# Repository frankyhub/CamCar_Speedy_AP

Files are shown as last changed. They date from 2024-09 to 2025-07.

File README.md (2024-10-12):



<div align="center">

|[:skull:ISSUE](https://github.com/frankyhub/CamCar_Speedy_AP/issues?q=is%3Aissue)|[:speech_balloon: Forum /Discussion](https://github.com/frankyhub/CamCar_Speedy_AP/discussions)|[:grey_question:WiKi](https://github.com/frankyhub/CamCar_Speedy_AP/wiki)||
|--|--|--|--|
| | | | |
||<a href="https://github.com/frankyhub/CamCar_Speedy_AP/issues">|<a href="https://github.com/frankyhub/CamCar_Speedy_AP/discussions">|<a href="https://github.com/frankyhub/CamCar_Speedy_AP/releases">|
|| <a href="https://github.com/frankyhub/CamCar_Speedy_AP/pulse" alt="Activity">| <a href="https://github.com/frankyhub/CamCar_Speedy_AP/graphs/traffic">  |<a href="https://github.com/frankyhub?tab=stars"> |
</div>

## Story

Diese Anleitung beschreibt ein Remote Controlled Car Robot mit Handy-Steuerung und Web-Cam. Der Antrieb erfolgt über zwei Getriebe-Motore, als Spannungversorgung dienen zwei Akkus oder optional eine Powerbank bzw. eine 9V-Batterie. Das Herzstrück ist ein ESP32-CAM, die Bodenplatte wird aus einer 4mm Sperrholzplatte gelasert. Nach anlegen der Versorgungsspannung startet das Programm mit einem Access Point (AP). Der AP wird in den WLAN-Einstellungen des Handy/Tablet aufgerufen und danach mit der IP-Adresse 192.168.4.1 der WEB-Server im Browser gestartet. Mit dem WEB-Server steht das Kammerabild und die Motor-Steuer-Buttons zur Verfügung.

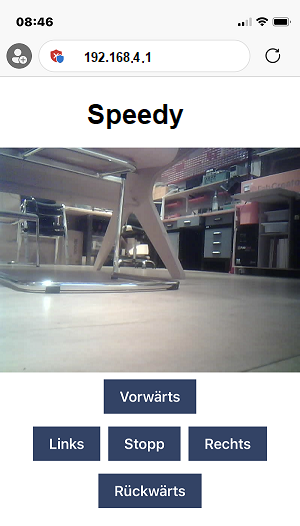
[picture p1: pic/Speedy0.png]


## Hardware

Die Stückliste für das CamCar:

| Anzahl | Bezeichnung | 
| --- | --- |
|  1 |  ESP32-CAM  |
|  1 |  ESP32-CAM Shield  |
| 1  |  Sperrholzplatte DINA4 4mm |
|  8 |  Platinenhalter (3D-Druck)  |
| 2  |  Getriebemotore mit Räder  |
| 1  |  Lenkrolle mit Abstandsplatte  |
| 1  | Schalter |
| 1  |  Dual-H-Brücke-DC-Motorantrieb L298N  |
| 2  |  18650 Akkus mit Akkucase (optional eine Powerbank oder 9V Batterie)  |
| |  Kleinmaterial, Schrauben, Muttern, Klemmen, Platinenstecker, Schaltdraht  |
| ---  | --- |

## Aufbau und Montage

Der Aufbau und die Montage des CamCars ist in mehrere Schritte unterteilt.

Schritt 1: Die Sperrholzplatte lasern

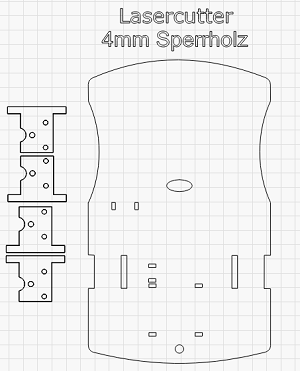
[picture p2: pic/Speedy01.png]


Schritt 2: Acht Platinenhalter drucken.

Die Platinenhalter tragen den ESP32 und die H-Brücke. Sie werden auf die Bodenplatte geklebt.

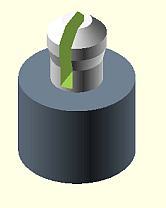
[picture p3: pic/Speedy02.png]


Schritt 3: Die vier Getriebemotore auf die Bodenplatte montieren (Senkkopfschrauben M3x30).

Die Lötfahnen zeigen jeweils nach innen.

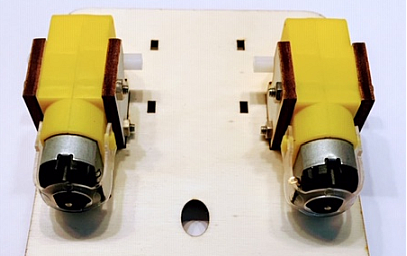
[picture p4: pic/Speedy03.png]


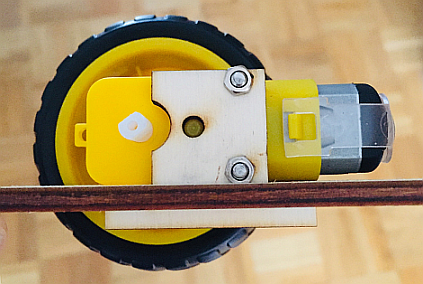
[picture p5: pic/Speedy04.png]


Schritt 4: Die Bauelemente nach Schaltplan verdrahten.

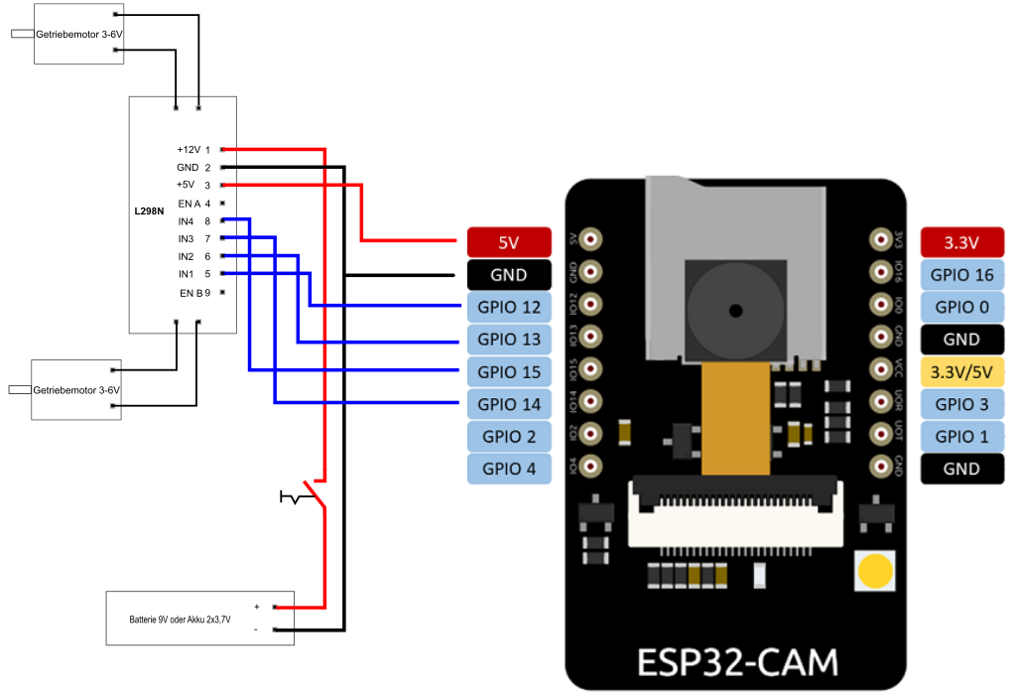
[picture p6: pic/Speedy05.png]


ESP32-CAM - L298N Verdahtung:

| L298N  | ESP32 | 
| --- | --- |
| IN1	  | 12 |
| IN2	  | 13 |
| IN3	  |  14  |
|  IN4	 |  15  |
| 5V	  | 5V	 |
| GND  |  GND  |
| ---  |  ---  |

Den ESP32 auf das ESP-Shield stecken und nach Schaltplan verdrahten.

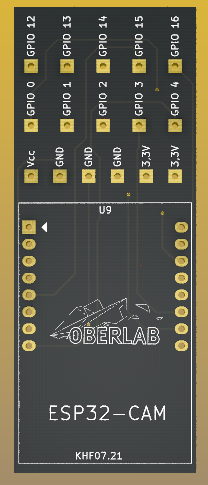
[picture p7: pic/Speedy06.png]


L298N Verdahtung:

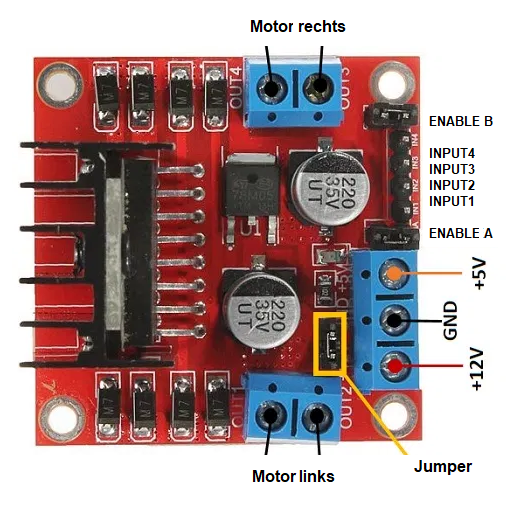
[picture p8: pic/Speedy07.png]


Schritt 5: Das Akku-Case und den Motor-Treiber L298N auf die Bodenplatte montieren. Den ESP32-CAM mit dem Shield auf die Oberseite montieren.

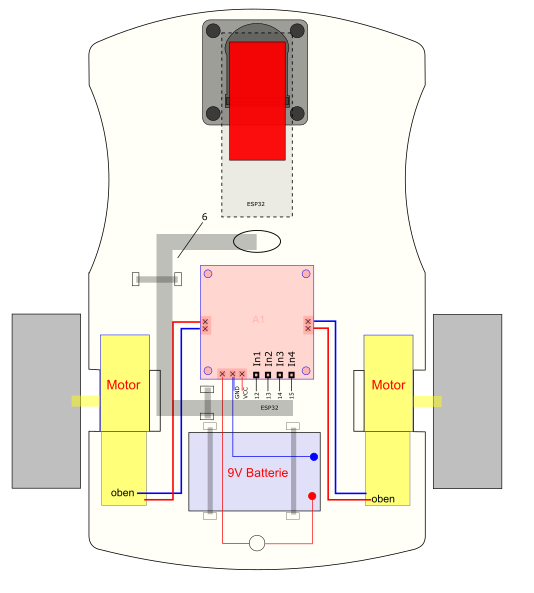
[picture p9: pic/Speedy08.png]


ESP32-CAM:

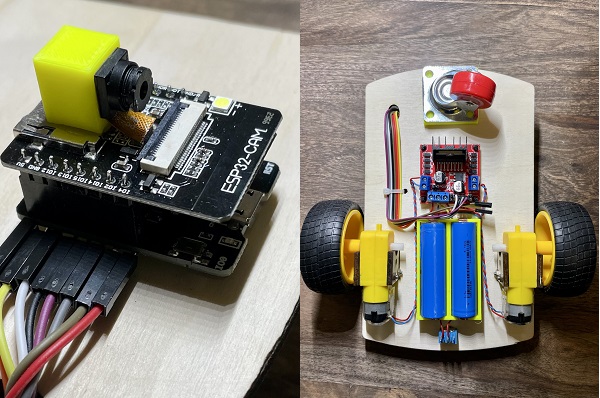
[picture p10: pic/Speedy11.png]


Schritt 6: Das vordere Lenkrad montieren und die beiden Räder auf die Getriebemotore stecken.

Schritt 7: Das Programm in den ESP32-CAM laden.

Schritt 8: In den WLAN Einstellungen des Handys/Tablet den ESP wählen und im Browser den WEB-Server mit der IP 192.168.4.1 aufrufen.

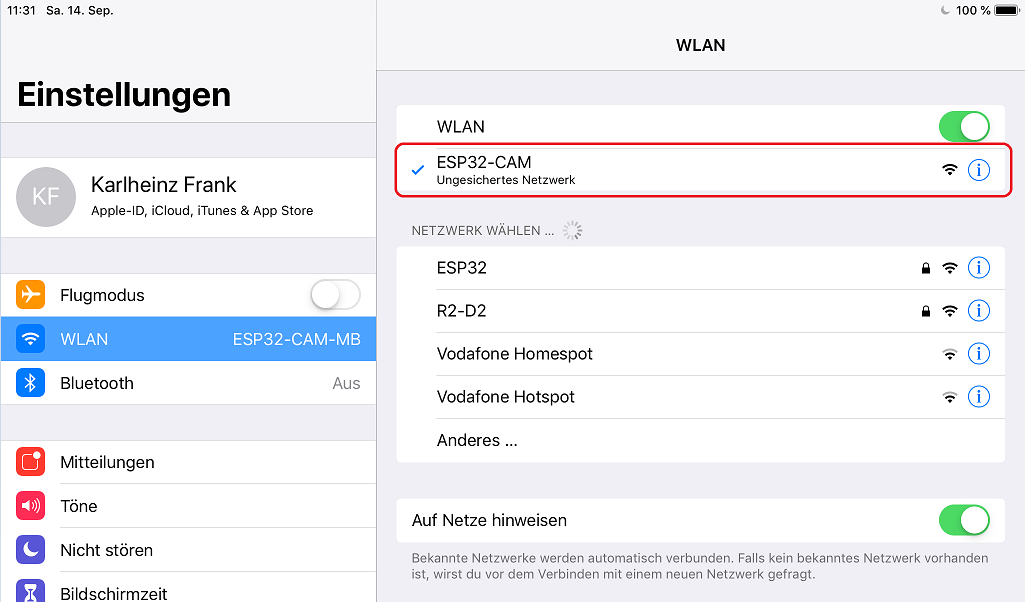
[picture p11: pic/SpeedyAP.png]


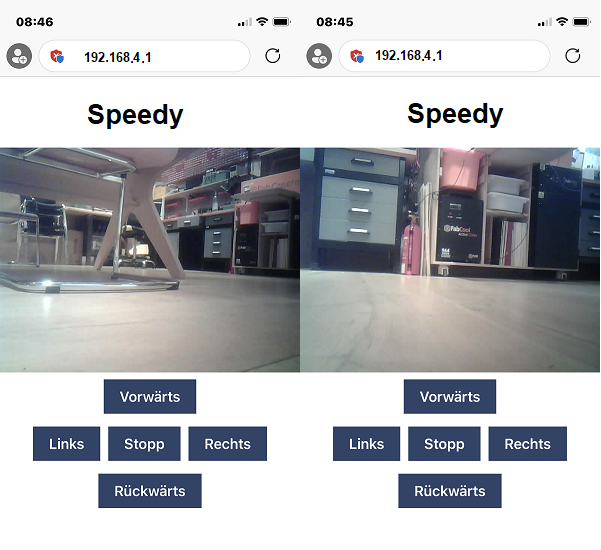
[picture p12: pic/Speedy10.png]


---

<div style="position:absolute; left:2cm; ">   
<ol class="breadcrumb" style="border-top: 2px solid black;border-bottom:2px solid black; height: 45px; width: 900px;"> <p align="center"><a href="#oben">nach oben</a></p></ol>
</div>  

---

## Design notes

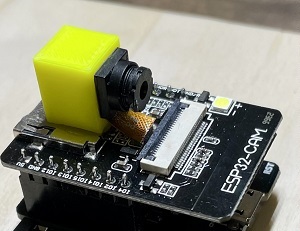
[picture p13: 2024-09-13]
pic/Speedy09.jpg

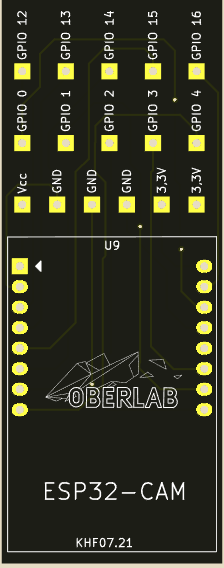
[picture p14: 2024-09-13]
kicad/Speedy/Speedy.png

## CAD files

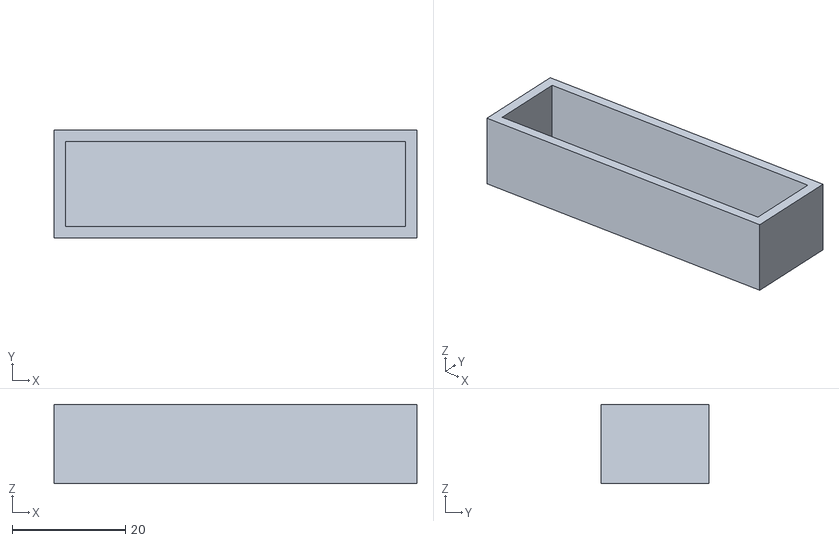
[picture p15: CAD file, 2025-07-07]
3D/AA_Case1.stl
64.0 x 19.0 x 14.0

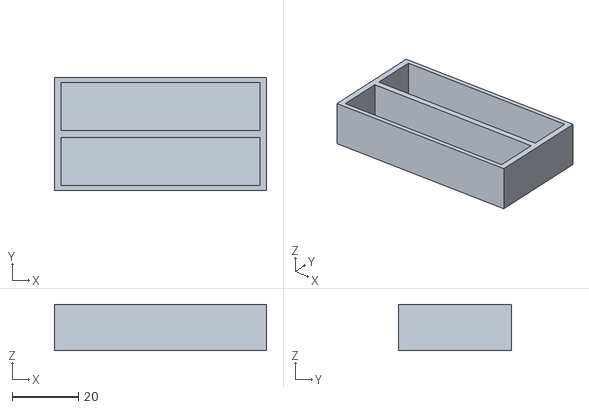
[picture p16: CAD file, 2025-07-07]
3D/AA_Case2.stl
64.0 x 34.0 x 14.0

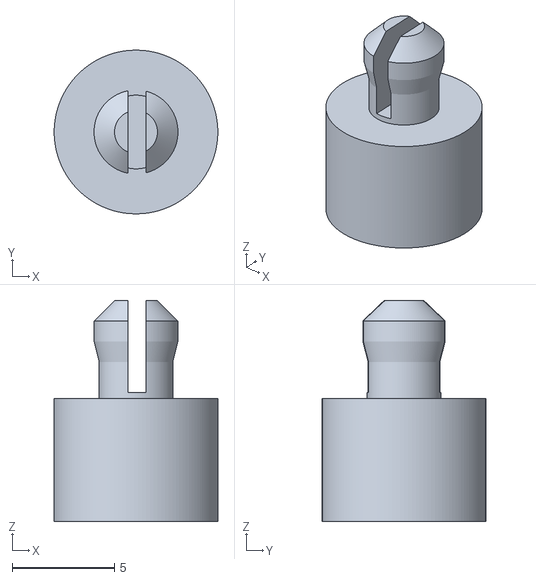
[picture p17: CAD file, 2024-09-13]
3D/PIN-4mm.stl
8.00 x 8.00 x 10.8

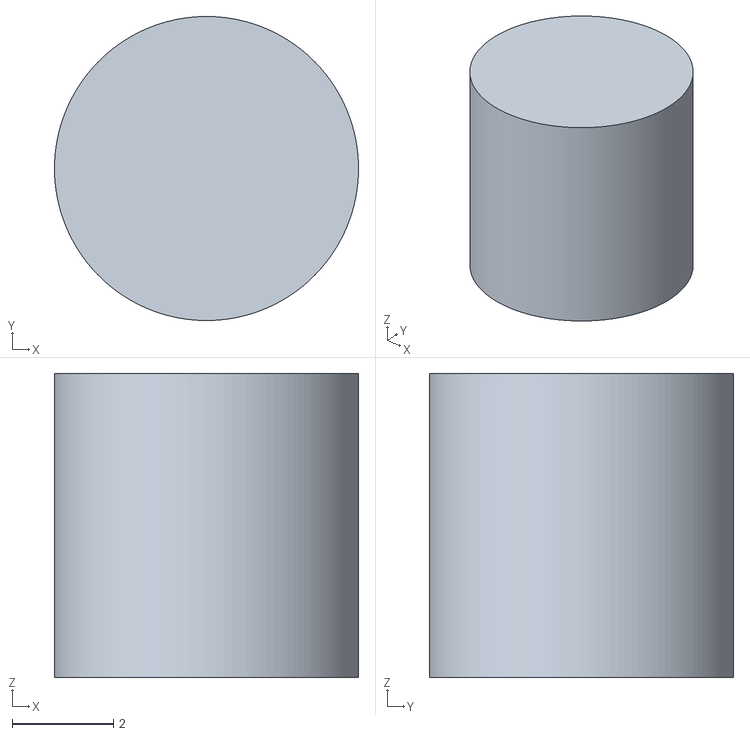
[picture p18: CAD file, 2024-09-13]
3D/ESP-PIN.stl
6.00 x 6.00 x 6.00

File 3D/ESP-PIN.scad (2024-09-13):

$fn=130;

D_sock=6;   //Sockeldurchmesser
D_knub=0; //Knubbeldurchmesser
H_sock=6;   //Sockelhöhe
H_knub=0   ;  //Knubbelhöhe 10 = Knuppelsockel=1.3mm
S_knub=0.5; //Schaftdurchmesser=Knubbeldurchmesser-0.5

//Sockel
H=H_sock-6;
color("SlateGray")
//color("WhiteSmoke")
translate([0,0,H*-1])
cylinder (h=H_sock, d=D_sock);

difference(){

//Knubbl
//color("SlateGray")
color("WhiteSmoke")    

union(){

translate([0,0,H_knub-0.7])
cylinder (h=1, d1=D_knub, d2=D_knub-2);

translate([0,0,H_knub-2.7])
cylinder (h=1, d1=D_knub-S_knub, d2=D_knub);

translate([0,0,H_knub-1.7])
cylinder (h=1, d1=D_knub, d2=D_knub);

//Schaft
translate([0,0,5.3])
cylinder (h=2.5, d=D_knub-S_knub);   
}


//Einschnitt
translate([-0.4,-2.5,6.3])
 cube([0.9,5,7]);
}

//Knuppel-Shaft messen V3 Höhe = 1.3mm
//translate([2,-3,6])
// cube([0.9,5,1.3]);

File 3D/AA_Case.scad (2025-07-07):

/*
*******************************************
Objekt Info: AA Batterie Box einfach/zweifach

*******************************************
Version: 11.07.2023 khf
*******************************************
*/

//***************   Auswahl   *************

        //Auswahl 1x Case oder 2x Case
        part="case2"; // case1, case2

//***************   Libraries  ************

//keine

//*****************************************

//***************  Parameter   *************
$fn=60;
//*****************************************

//**************   Programm  **************

//-----------------------------------
module case1(){
//Case 1x
 union(){
difference()
translate(v = [0, 21, 0])
difference(){
cube(size = [64,18,14], center = true);
translate(v = [0, 0, 1])
cube(size = [60,15,15], center = true);
}
}
}
//-----------------------------------

//-----------------------------------
module case2(){
//Case 1
 union(){
difference()
translate(v = [0, 21, 0])
difference(){
cube(size = [64,18,14], center = true);
translate(v = [0, 0, 1])
cube(size = [60,15,15], center = true);
}

}

//Case 2

difference()
translate(v = [0, 37, 0])
difference(){
cube(size = [64,18,14], center = true);
translate(v = [0, 0, 1])
cube(size = [60,15,15], center = true);
}
}
//-----------------------------------

//Part:

  if(part=="case1")
    case1();
  else if(part=="case2")
    case2();

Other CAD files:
3D/PIN_4mm.scad

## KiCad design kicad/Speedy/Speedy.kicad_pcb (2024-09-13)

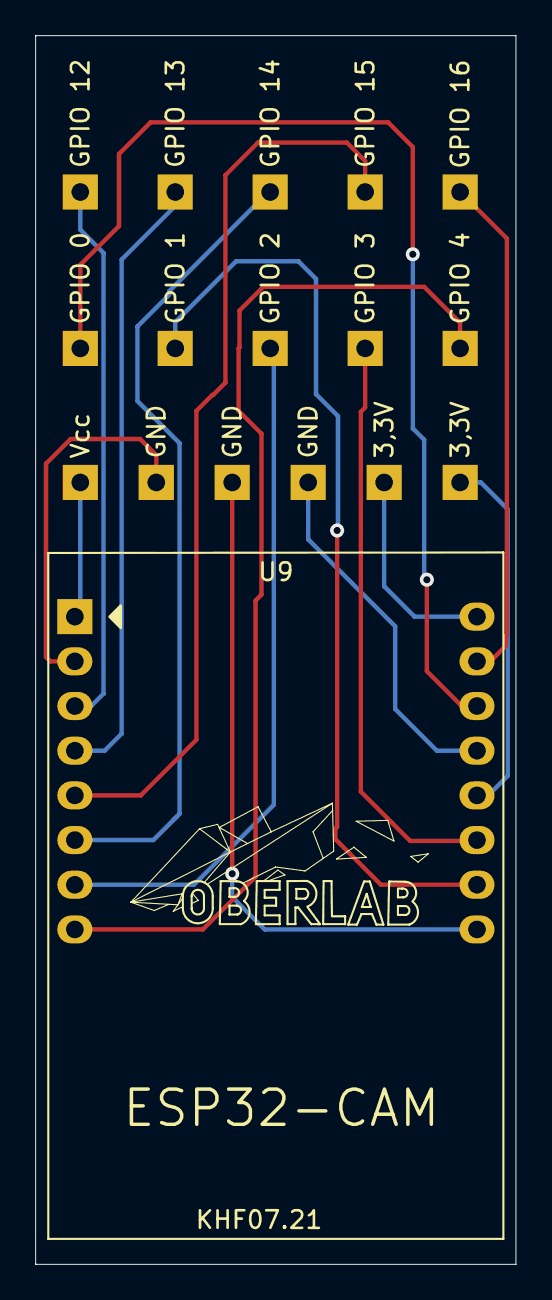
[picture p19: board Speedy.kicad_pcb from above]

Board: 2 copper layers, 27.3 x 69.8 mm, 17 parts (0 on the bottom side), 16 nets.

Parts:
3,3V, 3,3V#2: LP
GND: LP
GND#2, GND#3: LP
GPIO 0, GPIO 1, GPIO 2, GPIO 3, GPIO 4, GPIO 12, GPIO 13, GPIO 14, GPIO 15, GPIO 16: LP
U9: ESP32-CAM
Vcc: LP

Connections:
unnamed: U9.1, Vcc.1
unnamed: GND.1, U9.2
unnamed: GPIO 12.1, U9.3
unnamed: GPIO 13.1, U9.4
unnamed: GPIO 15.1, U9.5
unnamed: GPIO 14.1, U9.6
unnamed: GPIO 2.1, U9.7
unnamed: GPIO 4.1, U9.8
unnamed: 3,3V.1, U9.16
unnamed: GPIO 16.1, U9.15
unnamed: GPIO 0.1, U9.14
unnamed: GND#2.1, U9.13
unnamed: 3,3V#2.1, U9.12
unnamed: GPIO 3.1, U9.11
unnamed: GPIO 1.1, U9.10
unnamed: GND#3.1, U9.9

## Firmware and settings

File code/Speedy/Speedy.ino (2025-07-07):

/************************************************************************************************* 
                                      PROGRAMMINFO
************************************************************************************************** 
Funktion: Speedy mit AP 192.168.4.1 und WEB-Server
**************************************************************************************************
Version: 06.07.2025
**************************************************************************************************
Board:  AI Thinker ESP32-CAM (ESP32 Wrover Module) Ver.ESPRESSIF 3.0.4
https://raw.githubusercontent.com/espressif/arduino-esp32/gh-pages/package_esp32_index.json
http://arduino.esp8266.com/stable/package_esp8266com_index.json
https://adafruit.github.io/arduino-board-index/package_adafruit_index.json
**************************************************************************************************
C++ Arduino IDE V1.8.19
**************************************************************************************************
**************************************************************************************************
Librarys
- WiFi.h V0.16.1
- WebServer.h
 **************************************************************************************************/

#include "esp_camera.h"
#include <WiFi.h>
#include <WebServer.h>
#include "esp_timer.h"
#include "img_converters.h"
#include "Arduino.h"
#include "fb_gfx.h"
//#include "soc/soc.h"             // disable brownout problems
//#include "soc/rtc_cntl_reg.h"    // disable brownout problems
#include "esp_http_server.h"

const char* ssid = "Speedy";
const char* password = "1234";

WebServer server(80);

#define PART_BOUNDARY "123456789000000000000987654321"



// CAMERA_MODEL_AI_THINKER
  #define PWDN_GPIO_NUM     32
  #define RESET_GPIO_NUM    -1
  #define XCLK_GPIO_NUM      0
  #define SIOD_GPIO_NUM     26
  #define SIOC_GPIO_NUM     27
  
  #define Y9_GPIO_NUM       35
  #define Y8_GPIO_NUM       34
  #define Y7_GPIO_NUM       39
  #define Y6_GPIO_NUM       36
  #define Y5_GPIO_NUM       21
  #define Y4_GPIO_NUM       19
  #define Y3_GPIO_NUM       18
  #define Y2_GPIO_NUM        5
  #define VSYNC_GPIO_NUM    25
  #define HREF_GPIO_NUM     23
  #define PCLK_GPIO_NUM     22


#define MOTOR_1_PIN_1    14
#define MOTOR_1_PIN_2    15
#define MOTOR_2_PIN_1    13 
#define MOTOR_2_PIN_2    12

static const char* _STREAM_CONTENT_TYPE = "multipart/x-mixed-replace;boundary=" PART_BOUNDARY;
static const char* _STREAM_BOUNDARY = "\r\n--" PART_BOUNDARY "\r\n";
static const char* _STREAM_PART = "Content-Type: image/jpeg\r\nContent-Length: %u\r\n\r\n";

httpd_handle_t camera_httpd = NULL;
httpd_handle_t stream_httpd = NULL;

static const char PROGMEM INDEX_HTML[] = R"rawliteral(
<html>
  <head>
    <title>KHF CAM-CAR</title>
    <meta name="viewport" content="width=device-width, initial-scale=1">
    <style>
      body { font-family: Arial; text-align: center; margin:0px auto; padding-top: 30px;}
      table { margin-left: auto; margin-right: auto; }
      td { padding: 8 px; }
      .button {
        background-color: #2f4468;
        border: none;
        color: white;
        padding: 10px 20px;
        text-align: center;
        text-decoration: none;
        display: inline-block;
        font-size: 18px;
        margin: 6px 3px;
        cursor: pointer;
        -webkit-touch-callout: none;
        -webkit-user-select: none;
        -khtml-user-select: none;
        -moz-user-select: none;
        -ms-user-select: none;
        user-select: none;
        -webkit-tap-highlight-color: rgba(0,0,0,0);
      }
      img {  width: auto ;
        max-width: 100% ;
        height: auto ; 
      }
    </style>
  </head>
  <body>
    <h1>KHF CAM-CAR</h1>
    <img src="" id="photo" >
    <table>
      <tr><td colspan="3" align="center"><button class="button" onmousedown="toggleCheckbox('forward');" ontouchstart="toggleCheckbox('forward');" onmouseup="toggleCheckbox('stop');" ontouchend="toggleCheckbox('stop');">Vorw&auml;rts</button></td></tr>
      <tr><td align="center"><button class="button" onmousedown="toggleCheckbox('left');" ontouchstart="toggleCheckbox('left');" onmouseup="toggleCheckbox('stop');" ontouchend="toggleCheckbox('stop');">Links</button></td><td align="center"><button class="button" onmousedown="toggleCheckbox('stop');" ontouchstart="toggleCheckbox('stop');">Stopp</button></td><td align="center"><button class="button" onmousedown="toggleCheckbox('right');" ontouchstart="toggleCheckbox('right');" onmouseup="toggleCheckbox('stop');" ontouchend="toggleCheckbox('stop');">Rechts</button></td></tr>
      <tr><td colspan="3" align="center"><button class="button" onmousedown="toggleCheckbox('backward');" ontouchstart="toggleCheckbox('backward');" onmouseup="toggleCheckbox('stop');" ontouchend="toggleCheckbox('stop');">R&uuml;ckw&auml;rts</button></td></tr>                   
    </table>
   <script>
   function toggleCheckbox(x) {
     var xhr = new XMLHttpRequest();
     xhr.open("GET", "/action?go=" + x, true);
     xhr.send();
   }
   window.onload = document.getElementById("photo").src = window.location.href.slice(0, -1) + ":81/stream";
  </script>
  </body>
</html>
)rawliteral";

static esp_err_t index_handler(httpd_req_t *req){
  httpd_resp_set_type(req, "text/html");
  return httpd_resp_send(req, (const char *)INDEX_HTML, strlen(INDEX_HTML));
}

static esp_err_t stream_handler(httpd_req_t *req){
  camera_fb_t * fb = NULL;
  esp_err_t res = ESP_OK;
  size_t _jpg_buf_len = 0;
  uint8_t * _jpg_buf = NULL;
  char * part_buf[64];

  res = httpd_resp_set_type(req, _STREAM_CONTENT_TYPE);
  if(res != ESP_OK){
    return res;
  }

  while(true){
    fb = esp_camera_fb_get();
    if (!fb) {
      Serial.println("Camera capture failed");
      res = ESP_FAIL;
    } else {
      if(fb->width > 400){
        if(fb->format != PIXFORMAT_JPEG){
          bool jpeg_converted = frame2jpg(fb, 80, &_jpg_buf, &_jpg_buf_len);
          esp_camera_fb_return(fb);
          fb = NULL;
          if(!jpeg_converted){
            Serial.println("JPEG compression failed");
            res = ESP_FAIL;
          }
        } else {
          _jpg_buf_len = fb->len;
          _jpg_buf = fb->buf;
        }
      }
    }
    if(res == ESP_OK){
      size_t hlen = snprintf((char *)part_buf, 64, _STREAM_PART, _jpg_buf_len);
      res = httpd_resp_send_chunk(req, (const char *)part_buf, hlen);
    }
    if(res == ESP_OK){
      res = httpd_resp_send_chunk(req, (const char *)_jpg_buf, _jpg_buf_len);
    }
    if(res == ESP_OK){
      res = httpd_resp_send_chunk(req, _STREAM_BOUNDARY, strlen(_STREAM_BOUNDARY));
    }
    if(fb){
      esp_camera_fb_return(fb);
      fb = NULL;
      _jpg_buf = NULL;
    } else if(_jpg_buf){
      free(_jpg_buf);
      _jpg_buf = NULL;
    }
    if(res != ESP_OK){
      break;
    }
    //Serial.printf("MJPG: %uB\n",(uint32_t)(_jpg_buf_len));
  }
  return res;
}

static esp_err_t cmd_handler(httpd_req_t *req){
  char*  buf;
  size_t buf_len;
  char variable[32] = {0,};
  
  buf_len = httpd_req_get_url_query_len(req) + 1;
  if (buf_len > 1) {
    buf = (char*)malloc(buf_len);
    if(!buf){
      httpd_resp_send_500(req);
      return ESP_FAIL;
    }
    if (httpd_req_get_url_query_str(req, buf, buf_len) == ESP_OK) {
      if (httpd_query_key_value(buf, "go", variable, sizeof(variable)) == ESP_OK) {
      } else {
        free(buf);
        httpd_resp_send_404(req);
        return ESP_FAIL;
      }
    } else {
      free(buf);
      httpd_resp_send_404(req);
      return ESP_FAIL;
    }
    free(buf);
  } else {
    httpd_resp_send_404(req);
    return ESP_FAIL;
  }

  sensor_t * s = esp_camera_sensor_get();
  int res = 0;
  
  if(!strcmp(variable, "forward")) {
    Serial.println("Vorwärts");
    digitalWrite(MOTOR_1_PIN_1, 1); //1
    digitalWrite(MOTOR_1_PIN_2, 0); //0
    digitalWrite(MOTOR_2_PIN_1, 1); //1
    digitalWrite(MOTOR_2_PIN_2, 0); //0
  }
  else if(!strcmp(variable, "left")) {
    Serial.println("Links");
    digitalWrite(MOTOR_1_PIN_1, 0);
    digitalWrite(MOTOR_1_PIN_2, 1); //1
    digitalWrite(MOTOR_2_PIN_1, 0);
    digitalWrite(MOTOR_2_PIN_2, 0);
  }
  else if(!strcmp(variable, "right")) {
    Serial.println("Rechts");
    digitalWrite(MOTOR_1_PIN_1, 0); 
    digitalWrite(MOTOR_1_PIN_2, 0);
    digitalWrite(MOTOR_2_PIN_1, 0);  
    digitalWrite(MOTOR_2_PIN_2, 1); //1
  }
  else if(!strcmp(variable, "backward")) {
    Serial.println("Rückwärts");
    digitalWrite(MOTOR_1_PIN_1, 0); //0
    digitalWrite(MOTOR_1_PIN_2, 1); //1
    digitalWrite(MOTOR_2_PIN_1, 0); //0
    digitalWrite(MOTOR_2_PIN_2, 1); //1
  }
  else if(!strcmp(variable, "stop")) {
    Serial.println("Stopp");
    digitalWrite(MOTOR_1_PIN_1, 0);
    digitalWrite(MOTOR_1_PIN_2, 0);
    digitalWrite(MOTOR_2_PIN_1, 0);
    digitalWrite(MOTOR_2_PIN_2, 0);
  }
  else {
    res = -1;
  }

  if(res){
    return httpd_resp_send_500(req);
  }

  httpd_resp_set_hdr(req, "Access-Control-Allow-Origin", "*");
  return httpd_resp_send(req, NULL, 0);
}

void startCameraServer(){
  httpd_config_t config = HTTPD_DEFAULT_CONFIG();
  config.server_port = 80;
  httpd_uri_t index_uri = {
    .uri       = "/",
    .method    = HTTP_GET,
    .handler   = index_handler,
    .user_ctx  = NULL
  };

  httpd_uri_t cmd_uri = {
    .uri       = "/action",
    .method    = HTTP_GET,
    .handler   = cmd_handler,
    .user_ctx  = NULL
  };
  httpd_uri_t stream_uri = {
    .uri       = "/stream",
    .method    = HTTP_GET,
    .handler   = stream_handler,
    .user_ctx  = NULL
  };
  if (httpd_start(&camera_httpd, &config) == ESP_OK) {
    httpd_register_uri_handler(camera_httpd, &index_uri);
    httpd_register_uri_handler(camera_httpd, &cmd_uri);
  }
  config.server_port += 1;
  config.ctrl_port += 1;
  if (httpd_start(&stream_httpd, &config) == ESP_OK) {
    httpd_register_uri_handler(stream_httpd, &stream_uri);
  }
}

void setup() {
//  WRITE_PERI_REG(RTC_CNTL_BROWN_OUT_REG, 0); //disable brownout detector
  
  pinMode(MOTOR_1_PIN_1, OUTPUT);
  pinMode(MOTOR_1_PIN_2, OUTPUT);
  pinMode(MOTOR_2_PIN_1, OUTPUT);
  pinMode(MOTOR_2_PIN_2, OUTPUT);
  
  Serial.begin(115200);
  Serial.setDebugOutput(false);
  
  camera_config_t config;
  config.ledc_channel = LEDC_CHANNEL_0;
  config.ledc_timer = LEDC_TIMER_0;
  config.pin_d0 = Y2_GPIO_NUM;
  config.pin_d1 = Y3_GPIO_NUM;
  config.pin_d2 = Y4_GPIO_NUM;
  config.pin_d3 = Y5_GPIO_NUM;
  config.pin_d4 = Y6_GPIO_NUM;
  config.pin_d5 = Y7_GPIO_NUM;
  config.pin_d6 = Y8_GPIO_NUM;
  config.pin_d7 = Y9_GPIO_NUM;
  config.pin_xclk = XCLK_GPIO_NUM;
  config.pin_pclk = PCLK_GPIO_NUM;
  config.pin_vsync = VSYNC_GPIO_NUM;
  config.pin_href = HREF_GPIO_NUM;
  config.pin_sscb_sda = SIOD_GPIO_NUM;
  config.pin_sscb_scl = SIOC_GPIO_NUM;
  config.pin_pwdn = PWDN_GPIO_NUM;
  config.pin_reset = RESET_GPIO_NUM;
  config.xclk_freq_hz = 20000000;
  config.pixel_format = PIXFORMAT_JPEG; 
  
  if(psramFound()){
    config.frame_size = FRAMESIZE_VGA;
    config.jpeg_quality = 10;
    config.fb_count = 2;
  } else {
    config.frame_size = FRAMESIZE_SVGA;
    config.jpeg_quality = 12;
    config.fb_count = 1;
  }
  
  // Camera init
  esp_err_t err = esp_camera_init(&config);
  if (err != ESP_OK) {
    Serial.printf("Camera init failed with error 0x%x", err);
    return;
  }
 
  // ESP access point
  Serial.print("Access Point…");
  WiFi.mode(WIFI_AP);
  WiFi.softAP(ssid, password);
  IPAddress IP = WiFi.softAPIP();
  Serial.print("IP Adresse: ");
  Serial.println(IP);
  
 
  // Start streaming web server
  startCameraServer();
}

void loop() {
  
}
